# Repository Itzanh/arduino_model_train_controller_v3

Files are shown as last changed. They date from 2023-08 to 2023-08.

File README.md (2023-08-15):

# Arduino Model Train Controller V3

**IMPORTANT: WORK IN PROGRESS**

Arduino Model Train Controller is a program that controls model trains and adds full remote train traffic control: zone blocking, control of the switches, and manual control of the trains. This program focuses on controlling basic model trains modified by adding an Arduino Nano or similar flashed with this software to give the Arduino full control of the model train. This would allow the user to have the full functionality of a remote-controller rail-powered model train in a basic battery-powered model train with no remote control capabilities built-in that has been modified with this software.

The required components to modify the model train are:
- Arduino Nano (or similar)
- HC-05: Bluetooth module that keeps the Arduino in contact with the computer
- L293D chip: to control the built-in motor of the model train
- Reed switch: to detect magnets along the tracks (explained below)
- LED (optional): for train-tracks communication
- Photoresistor (optional): for train-tracks communication

The method to divide the tracks into zones is done by adding small magnets to the tracks (normally by taping them), and attaching a reed switch to the bottom of the model trains. The computer software knows where the trains are because every time they encounter a magnet, they notify the computer and the computer counts the magnets.

## Architecture

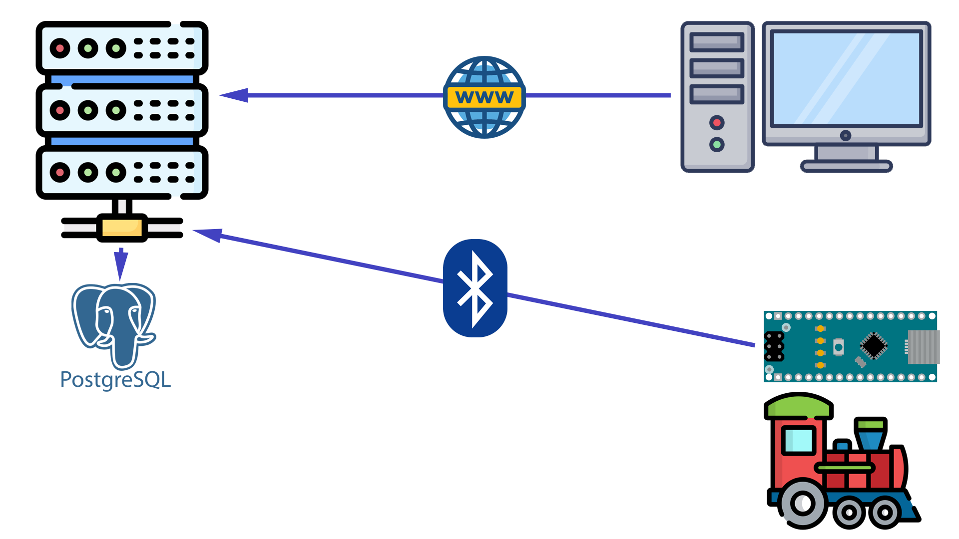
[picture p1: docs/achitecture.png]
graph of the architecture described below


This software is divided in three parts: the server, the web application, and the Arduino sketch.

The server is made with GoLang, and it does all the heavy thinking to control the traffic of the trains. It receives connections from the web application and from the model trains. This server requires to have PostgreSQL installed to work.

The web application is made with react, it connects to the server through WebSocket and allows the end user to dispatch trains and control traffic, among other things.

The Arduino sketch is made to be run in an Arduino Nano or similar, and expects a specific pinout and connections. This is described in the "Modifying the toy train" section below. This software must be flashed to the microcontroller using the Arduino IDE.

## Software installation

### Installing PostgreSQL

Download and install PostgreSQL in your system, create a new database and create a user with access to the database.

### Installing the server

Browse to the server's root folder and run the following command:

```bash
go build -o main.exe | .\main.exe
```

### Installing the web application

Browse to the web application's root folder and run the following command:

```bash
npm run-script build
```

And copy the contents of the "build" folder into a web server's root folder.

### Setting up the trains, zones and signals

#### Set up the trains

Go into the web application into the Trains tab. Use the add button to add as much trains are you are going to use. The three speeds are between 1 and 255, and have to follow this rule: 1 <= slow < half < fast <= 255. In this speeds, 1 means the slowest speed that the train can go (set by the *MOTOR_MIN_POWER* constant explained below) and 255 means the fastest speed that the train can go (set by the *MOTOR_MAX_POWER* constant explained below).

#### Set up the stretches

Stretches are separate zones of tracks, normally independent areas interconnected by switches. Stretches can be set up from the Stretches tab in the web application, added using the add button.

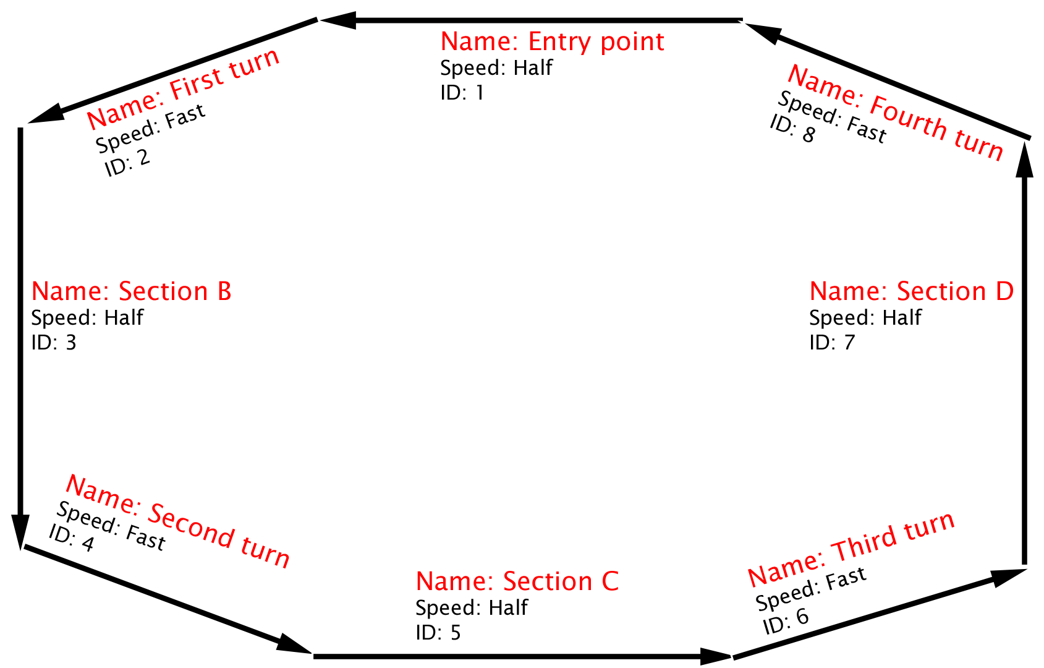
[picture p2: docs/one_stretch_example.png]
example of a circuit with only one stretch


For example, in the model above there is only one stretch.

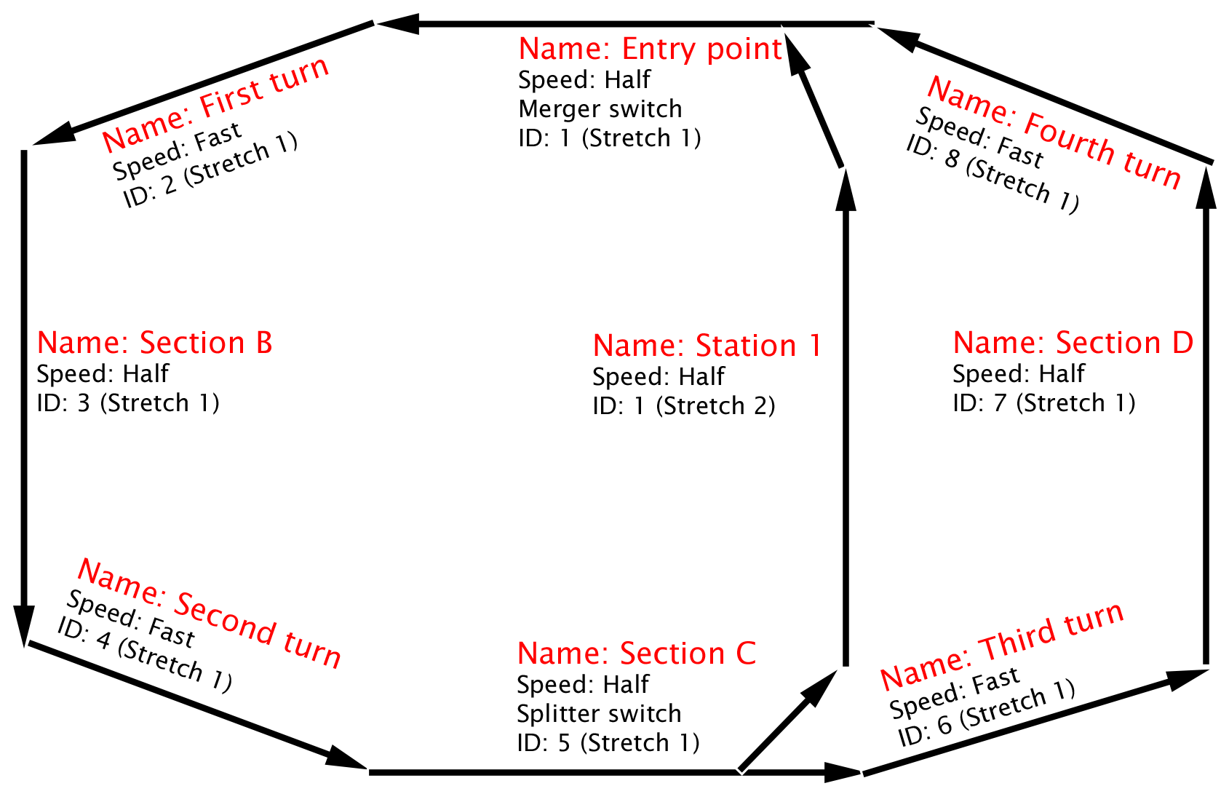
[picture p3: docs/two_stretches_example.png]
example of a circuit with two stretch


For example, in the model above there are two stretches, separated by switches.

#### Set up the signals

Signals are like semaphores, they are used to keep the trains from entering zones occupied by other trains.
When a train put in the model, the user has to manually input the zone that the train is left at, and then the software will keep tracks of where the train is by counting the times that the train reports magnets in the tracks. Every time a train detects a magnet, it passes a signal (or semaphore), therefore there have to be registered as many signals in the program as magnets there are in the tracks.

The way that the software will use this is that only one train at a time will be allowed in the zone between two magnets. If a train steps on a magnet, and the next zone is occupied, the software tells the train to stop and when the zone is freed, it automatically tells the stopped train to start again.

Also different zones can have different speed limits, set by the user, that will automatically be sent from the software to the trains.

The distance between the magnets can never be lower than the maximum length that is expected from a train, as the software considers that, when the train enters a new zone, it has therefore completely exited the zone where it was before and is available to be occupied by another train.

Additionally, some of the zones can be set up as switches, which can be splitters or mergers. In the case of setting the zone as a splitter, the stretch and signal id required will be the signal to which the train will be sent to in case that the switch is flipped to the detour position. In case that it's set as a merger (not splitter), the stretch and signal id required will be the signal from which it will merge from in case that the switch is flipped to the detour position.

In case that your circuit is a loop, you can set a signal to loop back to another signal by entering the required stretch and signal id.

## Hardware

### Modifying the toy train

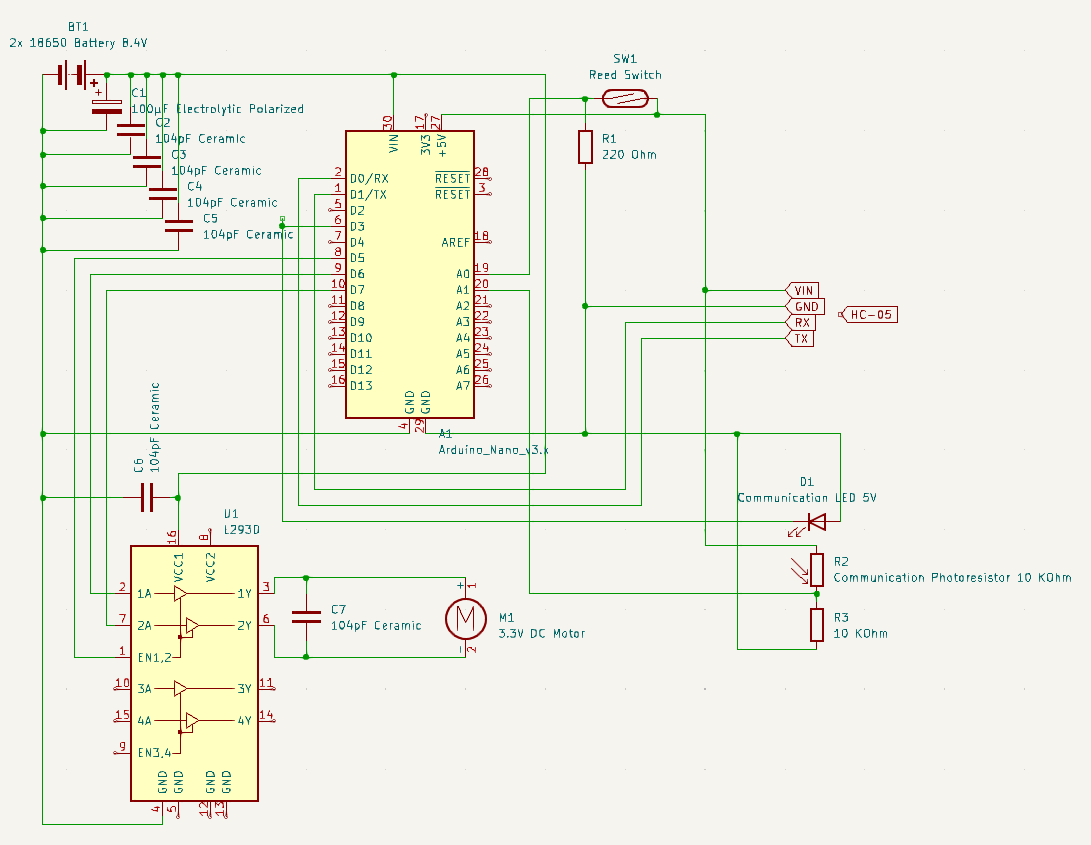
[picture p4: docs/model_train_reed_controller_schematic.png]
Schematic of the model train circuit controller


Schematics are provided in the docs folder of the circuit that the included sketch expects.

In this schematic, the power supply are two 18650 rechargeable lithium-ion batteries (recommended) (BT1), that provide a voltage of 8.4V when fully charged. This is fed directly to the VIN and GND pins of the Arduino (A1), and to the VCC1 and GND pins of the L293D (U1, motor controller chip).

Pinout for the L293D chip:

| L293D pin | Connection |
|---|---|
| PIN#1 | Arduino PIN D5 |
| PIN#2 | Arduino PIN D6 |
| PIN#3 | Toy train motor + |
| PIN#4 | Battery ground |
| PIN#6 | Toy train motor - |
| PIN#7 | Arduino PIN D7 |
| PIN#8 | 8.4V from the battery |

The capacitors are optional, but the ceramic ones are recommended in order to reduce the noise generated by the motor. The values might be others as long as they are reasonable.

The reed switch (SW1) must be placed (for example, taped) to the bottom of the train, in order for it to detect the magnets the are along the tracks. One side of the reed switch has to be connected to 5V (or the logic level of the microcontroller used), and the other side has to be connected to the analog pin #0 of the microcontroller and tied to ground though a resistor (R1) (anything between 100 to 1.000 Ohm should work).

The HC-05 Bluetooth module has to be connected to 5V (or the logic level of the microcontroller used) and ground (shared with the microcontroller's ground). Then, the microcontroller's serial TX pin has to be connected to the HC-05's RX, and vice versa. The HC-05 Bluetooth module has to be set to a UART baud rate of 57.600 beforehand. If you don't know how to do this or don't want to do it, you can also set the constant *SERIAL_BAUD_RATE* to 9.600 (default for the HC-05) in the sketch.

Optionally, the train has the ability to use LED blinks to communicate with other microcontrollers in the tracks that controls the switches, as it's described in the "Making the switch controllers" section below. The negative side of the LED (D1) has to be connected to ground (shared with the microcontroller's ground), and the positive side of the LED has to be connected to the microcontroller's D3 pin. The LED shouldn't need a resistor, because it's only going to be used momentarily, and also because we want it as bright as possible to communicate with the other microcontroller. Then, one side of the photoresistor (R2) has to be connected to 5V (or the logic level of the microcontroller used), and the other side has to be connected to the analog pin #1 of the microcontroller and tied to ground though a 10 KOhmn resistor (R3).

#### Adjusting the constants

- ACCESS_KEY: Key given by the web application when a train is registered.
- MOTOR_MAX_POWER: Number between 0 and 255. You can get it by using the following formula:
```
(Battery voltage / 255) * MOTOR_MAX_POWER = Motor voltage
```
For example, to run a 3V (2xAA battery) train with 2x 18650 batteries, MOTOR_MAX_POWER should be set to 91.
- MOTOR_MIN_POWER: Number between 0 and 255. Should always be lower than *MOTOR_MAX_POWER*. This is the lowest voltage at which the train will run for its lowest speed.
- THRESHOLD_UPPER: Used to detect the LED blinks with the photoresistor. The value reported by the ADC must be above this level to detect a HIGH level in the LED. The default value (800) is selected with a 10-bit ADC in mind.
- THRESHOLD_LOWER: Used to detect the LED blinks with the photoresistor. The value reported by the ADC must be below this level to detect a LOW level in the LED. The default value (400) is selected with a 10-bit ADC in mind.

### Making the switch splitteer controllers

Switch controllers are devices that be placed along the switches in the tracks and control the direction of a switch. They receive commands and communicate with the train using LEDs and photoresistors. In order to flip a switch, the software in the computer has to order the train to flip the switch, then the train will send the command to flip (either to the straight or detour position) to the switch controller via an LED aboard the train, and the blinks of the LED will be picked up by the photoresistor of the switch controller. Once the operation is completed, or if it fails, the switch controller will report it back to the train using the controller's LED and the train's photoresistor, so that the train can report that status back to the software in the computer.

These switch controllers have to be placed in front of where the LED and photoresistor are going to be with the train stopped at the magnet just before the switch, so the LEDs from one and the photoresistors of the other are face to face.

#### Communication protocol

All the messages sent through the LEDs follow a pattern of: ON, OFF, ON, OFF, and the time that the LED has spent ON the first time, then the time that it has spent OFF, and finally the time that is has spent ON the second time, will tell what message has been transmitted.

Messages that the train can transmit:

| Message | Time ON μs | Time OFF μs | Time ON μs |
|---|---|---|---|
| Switch to straight | 500.000 | 500.000 | 500.000 |
| Switch to detour | 1.500.000  | 1.500.00 | 1.500.000  |

Messages that the switch can transmit:

| Message | Time ON μs | Time OFF μs | Time ON μs |
|---|---|---|---|
| Switching successful | 500.000 | 1.500.000 | 500.000 |
| Switching failed | 1.500.000  | 500.00 | 1.500.000  |

It is recommended that a margin of error is applied, detecting everything between 300.000μs to 700.000μs as 500.000μs, and everything from 1.300.000μs to 1.700.000μs as 1.500.000μs. Also a 5s timeout during the message reception is recommended.

#### Manual controllers

Manual switch controllers are a type of switch controllers that can't physically flip the switch in the tracks, so they just take the order and turn on an LED to tell the user that the switch is to be flipped, and then the user has to manually actuate the switch and press a push button so the manual switch controller can send the successful command back to the train.

Required hardware:
- 1x Photoresistor
- 4x LED
- 1x Button
- 1x 10KOhm resistor
- 3x 220Ohm resistor

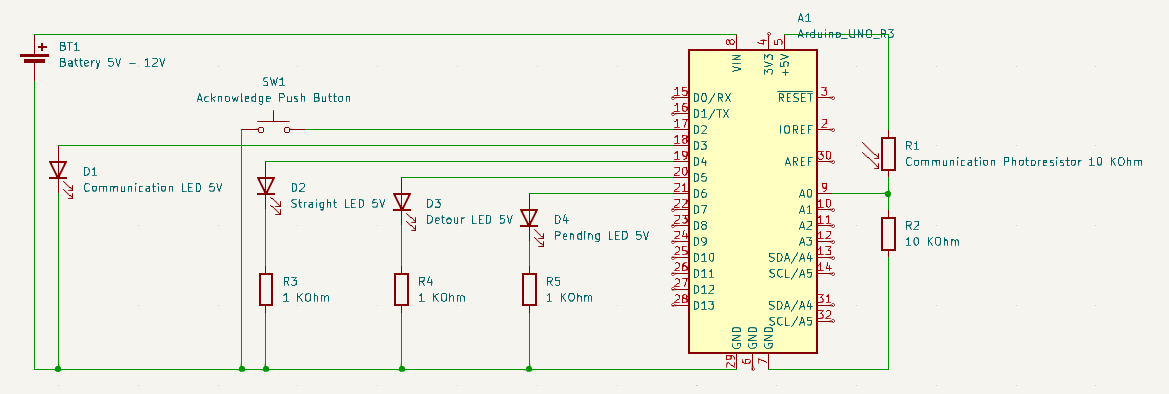
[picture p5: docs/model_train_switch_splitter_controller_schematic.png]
Schematics of the manual switch controller described below


Schematics are provided in the docs folder of the circuit that the included sketch expects.

The power supply may be everything that can power up your microcontroller, although because it has to be made easy to be portable in order to be placed and removed from the tracks easily, a 9V battery or a case with AA batteries might be a good power supply.

The negative side of the LED (D1) has to be connected to ground (shared with the microcontroller's ground), and the positive side of the LED has to be connected to the microcontroller's D3 pin. The LED shouldn't need a resistor, because it's only going to be used momentarily, and also because we want it as bright as possible to communicate with the other microcontroller. Then, one side of the photoresistor (R1) has to be connected to 5V (or the logic level of the microcontroller used), and the other side has to be connected to the analog pin #0 of the microcontroller and tied to ground though a 10 KOhmn resistor (R2).

A push button has to be connected from the microcontroller's D2 pin to ground. This will be the acknowledge button, that the user will have to press once the user has manually actuated the switch.

The pins D4, D5 and D6 will be connected to the positive sides of three LEDs that will be connected to ground through 3 220 Ohm resistors (although anything between 100 to 1.000 Ohm should work fine).

The LED connected to D4 will be the "straight" LED, and will tell the user that the switch is in the "straight position", and the one on D5 will be the "detour" LED to tell the user that this is the position that the switch is in. The LED connected to D6 will be the "needs to be switched" or "pending" LED. If the "pending" LED is on, then the position shown by the first two LEDs is the position that the switch **wants to be**, for example, if both the D4 ad D6 are lit, that means that the user has to move the switch to the straight position and press the acknowledge button.

#### Servomotor controllers

**WORK IN PROGRESS**

#### Stepper motor controllers

**WORK IN PROGRESS**

#### Solenoid motor controllers

**WORK IN PROGRESS**

### Making the switch merger controllers

#### Manual controllers

**WORK IN PROGRESS**

#### Servomotor controllers

**WORK IN PROGRESS**

#### Stepper motor controllers

**WORK IN PROGRESS**

#### Solenoid motor controllers

**WORK IN PROGRESS**

## Contributing

Pull requests are welcome. For major changes, please open an issue first
to discuss what you would like to change.

Please make sure to update tests as appropriate.

## Attribution

Some images and icons are from FlatIcon at [flaticon.com](flaticon.com).

## License

This code is distributed under the [AGPL](https://spdx.org/licenses/AGPL-3.0-only.html) license (AGPL-3.0-only).

You can find the full text of this license in the `COPYING` file.

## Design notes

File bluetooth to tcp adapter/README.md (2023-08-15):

# Model Train Controller

Open Model Train Controller is a software that can control different types of model trains from a computer through a browser, letting you become a “train dispatcher" of you model.

This software can control the signals of the model through microcontroller units (like Arduino, etc.) that are connected then to the computer. This software is entirely open source and free software published under the GNU AGPL license.

The code for the web dispatching interface, the server, and the code necessary for the microcontroller units are included in the repositories.

## Links

[Wiki - Documentation](http://izcloud.tk:5000/en/home)

[Model Train Controller Server Repository](https://gitlab.com/itzanh/model-train-controller-server)

[Model Train Controller Web Repository](https://gitlab.com/itzanh/model-train-controller-web)

[Model Train Controller Repository](https://gitlab.com/itzanh/model-train-controller)

[Model Train Controller Signal Controller Repository](https://gitlab.com/itzanh/model-train-controller-signal-controller)

[Model Train Controller Serial to TCP Repository](https://gitlab.com/itzanh/model-train-controller-serial-to-tcp)

[Model Train Controller I2C to Serial Repository](https://gitlab.com/itzanh/model-train-controller-i2c-to-serial)

## Contributing
Pull requests are welcome. For major changes, please open an issue first to discuss what you would like to change.

## License

This code is distributed under the [AGPL](https://spdx.org/licenses/AGPL-3.0-only.html) license (AGPL-3.0-only).

You can find the full text of this license in the `COPYING` file.

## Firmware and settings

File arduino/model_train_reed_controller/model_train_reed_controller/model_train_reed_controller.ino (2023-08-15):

/*
This file is part of Arduino Model Train Controller V3 (https://github.com/Itzanh/arduino_model_train_controller_v3).

Arduino Model Train Controller V3 is free software: you can redistribute it and/or modify it under the terms of the GNU Affero General Public License as published by the Free Software Foundation, version 3 of the License.

Model Train Controller is distributed in the hope that it will be useful, but WITHOUT ANY WARRANTY; without even the implied warranty of MERCHANTABILITY or FITNESS FOR A PARTICULAR PURPOSE. See the GNU Affero General Public License for more details.

You should have received a copy of the GNU Affero General Public License along with Model Train Controller. If not, see <https://www.gnu.org/licenses/>.
*/

// This sketch is made to be run on an Arduino Nano, with the objective to to control a model train, controlling its onboard-motor with a L293D-chip, detecting its position
// in the tracks using magnets left along the way in the tracks in specific positions, and receiving instructions for traffic control and signaling from a computer software
// that keeps communication with the Nano through a HC-05 Bluetooth module.
//
// Pinout description: (ARDUINO UNO / NANO)
// DIGITAL:
// 2
// 3 } - Communication LED
// 4
// 5   } - L293D - { Enable (~PWM) 10Ohm
// 6   }           { DIR_B 5.2KOhm
// 7   }           { DIR_A 5.2KOhm
// 8
// 9
// 10
// 11
// 12
// 13
// A0 } - Reed switch 5V / 220Ohm to GND
// A1 } - Photoresistor 5V / 10KOhm to GND
// TX -> HC-05 RX
// RX -> HC-05 TX



// Constants
const unsigned long ACCESS_KEY = 2107106630;
// const unsigned long ACCESS_KEY = 2086438159;
// const byte MOTOR_MAX_POWER = 100;
// const byte MOTOR_MIN_POWER = 85;
// const byte MOTOR_MAX_POWER = 120;
// const byte MOTOR_MIN_POWER = 85;
// const byte MOTOR_MAX_POWER = 190;
// const byte MOTOR_MIN_POWER = 85;
const byte MOTOR_MAX_POWER = 255;
const byte MOTOR_MIN_POWER = 85;
// const byte MOTOR_MIN_POWER = 200;
const float MAX_SPEED_LIMIT = 255;
const unsigned short SOFTWARE_DEBOUNCING_WAIT = 250; // ms
const unsigned short SERIAL_BAUD_RATE = 57600;
const unsigned short THRESHOLD_UPPER = 800;
const unsigned short THRESHOLD_LOWER = 400;

// DEFINE PINOUT
// Digital
const byte COMMUNICATION_LED_PIN = 3;
const byte MOTOR_ENABLE_PIN = 5;
const byte MOTOR_DIR_A_PIN = 6;
const byte MOTOR_DIR_B_PIN = 7;
// Analog
const byte REED_SWITCH_PIN = A0;
const byte ANALOG_PHOTORESISTOR_PIN = A1;



// Variables
volatile bool reedSwitchClosed = false;
volatile long lastReedSwitchClosedTime = 0;



enum CommunicationMessageServerToClient {
  FORWARD = 1,
  BACKWARD = 2,
  FAST_STOP = 3,
  SWITCH_PASSTHROUGH = 4,
  SWITCH_DETOUR = 5,
};

enum CommunicationMessageClientToServer {
  REED_TRIGGERED = 1,
  SWITCH_SUCCESS = 2,
  SWITCH_FAILURE = 3,
};

void setup()
{
  pinMode(COMMUNICATION_LED_PIN, OUTPUT);

  // Initialize the pins for the L293D motor controller
  pinMode(MOTOR_ENABLE_PIN, OUTPUT);
  pinMode(MOTOR_DIR_A_PIN, OUTPUT);
  pinMode(MOTOR_DIR_B_PIN, OUTPUT);

  // Open a (hardware) serial connection with the HC-05 BlueTooth module
  Serial.begin(SERIAL_BAUD_RATE);
  // Log in the the ground control software through BlueTooth
  blueToothLogin();
}

void blueToothLogin()
{
  // When the ground control server is ready, it sends a byte of all ones (255) and awaits for the token
  // Wait for the "ready" byte to come
  while (Serial.available() == 0) {}
  Serial.read();
  // Send the authentication token
  Serial.write((byte*)&ACCESS_KEY, sizeof(unsigned long));
}

void loop()
{
  if (reedSwitchClosed)
  {
    reedSwitchClosed = analogRead(REED_SWITCH_PIN) >= 256;
  }
  else
  {
    if ((analogRead(REED_SWITCH_PIN) > 512) && (millis() - lastReedSwitchClosedTime > 1000))
    {
      Serial.write(1);
      Serial.write(CommunicationMessageClientToServer::REED_TRIGGERED);
      reedSwitchClosed = true;
      lastReedSwitchClosedTime = millis();
    }
  }

  while (Serial.available())
  {
    receiveIncomingCommunicationMessage();
  }
}

void receiveIncomingCommunicationMessage()
{
  byte size = Serial.read();
  byte message[size];

  for (byte i = 0; i < size; i++) {
    int b = Serial.read();
    if (b == -1)
    {
      i--;
    }
    else
    {
      message[i] = b;
    }
  }

  processIncomingMessage(message);
}

void processIncomingMessage(byte message[])
{
  switch (message[0])
  {
    case CommunicationMessageServerToClient::FORWARD:
      {
        goForward(message[1]);
        break;
      }
    case CommunicationMessageServerToClient::BACKWARD:
      {
        goBackwards(message[1]);
        break;
      }
    case CommunicationMessageServerToClient::FAST_STOP:
      {
        fastStop();
        break;
      }
    case CommunicationMessageServerToClient::SWITCH_PASSTHROUGH:
      {
        switchToPassthrough();
        break;
    } case CommunicationMessageServerToClient::SWITCH_DETOUR:
      {
        switchToDetour();
        break;
      }
  }
}

void goForward(byte speedLimit)
{
  lastReedSwitchClosedTime = millis();
  byte motorSpeed = convertSpeedLimitToMotorSpeed(speedLimit);
  analogWrite(MOTOR_ENABLE_PIN, motorSpeed);
  digitalWrite(MOTOR_DIR_A_PIN, HIGH);
  digitalWrite(MOTOR_DIR_B_PIN, LOW);
}

void goBackwards(byte speedLimit)
{
  lastReedSwitchClosedTime = millis();
  byte motorSpeed = convertSpeedLimitToMotorSpeed(speedLimit);
  analogWrite(MOTOR_ENABLE_PIN, motorSpeed);
  digitalWrite(MOTOR_DIR_A_PIN, LOW);
  digitalWrite(MOTOR_DIR_B_PIN, HIGH);
}

void fastStop()
{
  analogWrite(MOTOR_ENABLE_PIN, 255);
  digitalWrite(MOTOR_DIR_A_PIN, LOW);
  digitalWrite(MOTOR_DIR_B_PIN, LOW);
}

byte convertSpeedLimitToMotorSpeed(byte speedLimit)
{
  float relativeSpeed = float(speedLimit) / MAX_SPEED_LIMIT;
  return MOTOR_MIN_POWER + (relativeSpeed * (MOTOR_MAX_POWER - MOTOR_MIN_POWER));
}

void switchToPassthrough() {
  digitalWrite(COMMUNICATION_LED_PIN, HIGH);
  delay(500);
  digitalWrite(COMMUNICATION_LED_PIN, LOW);
  delay(500);
  digitalWrite(COMMUNICATION_LED_PIN, HIGH);
  delay(500);
  digitalWrite(COMMUNICATION_LED_PIN, LOW);

  processLEDResponse();
}

void switchToDetour() {
  digitalWrite(COMMUNICATION_LED_PIN, HIGH);
  delay(1500);
  digitalWrite(COMMUNICATION_LED_PIN, LOW);
  delay(1500);
  digitalWrite(COMMUNICATION_LED_PIN, HIGH);
  delay(1500);
  digitalWrite(COMMUNICATION_LED_PIN, LOW);

  processLEDResponse();
}

void processLEDResponse()
{
  if (waitForLEDResponse())
  {
    Serial.write(1);
    Serial.write(CommunicationMessageClientToServer::SWITCH_SUCCESS);
  }
  else
  {
    Serial.write(1);
    Serial.write(CommunicationMessageClientToServer::SWITCH_FAILURE);
  }
}

bool waitForLEDResponse() {
  // Wait for it to go HIGH
  /*do {

    } while (analogRead(ANALOG_PHOTORESISTOR_PIN) <= THRESHOLD_LOWER);*/
  do {

  } while (analogRead(ANALOG_PHOTORESISTOR_PIN) <= THRESHOLD_UPPER);
  // It went HIGH, note the time and wait for it to go LOW again
  unsigned long startMicros = micros();
  unsigned long timeoutMillis = millis() + 5000;
  do {
    if (millis() >= timeoutMillis) {
      // Serial.println("TIMEOUT 1");
      /*Serial.write(3);
      Serial.write(128);
      Serial.write("F");
      Serial.write(1);*/
      return false;
    }
  } while (analogRead(ANALOG_PHOTORESISTOR_PIN) <= THRESHOLD_UPPER);
  do {
    if (millis() >= timeoutMillis) {
      // Serial.println("TIMEOUT 2");
      /*Serial.write(3);
      Serial.write(128);
      Serial.write("F");
      Serial.write(2);*/
      return false;
    }
  } while (analogRead(ANALOG_PHOTORESISTOR_PIN) >= THRESHOLD_LOWER);
  // It went HIGH and then LOW again
  unsigned long endMicros = micros();
  unsigned long microsPeriod1 = endMicros - startMicros;
  timeoutMillis = millis() + 5000;
  // Wait for it to go HIGH again
  do {
    if (millis() >= timeoutMillis) {
      // Serial.println("TIMEOUT 3");
      /*Serial.write(3);
      Serial.write(128);
      Serial.write("F");
      Serial.write(3);*/
      return false;
    }
  } while (analogRead(ANALOG_PHOTORESISTOR_PIN) <= THRESHOLD_UPPER);
  // It went HIGH again, note the time that it spent LOW and note the start time
  unsigned long microsPeriod2 = micros() - endMicros;
  startMicros = micros();
  timeoutMillis = millis() + 5000;
  do {
    if (millis() >= timeoutMillis) {
      // Serial.println("TIMEOUT 4");
      /*Serial.write(3);
      Serial.write(128);
      Serial.write("F");
      Serial.write(4);*/
      return false;
    }
  } while (analogRead(ANALOG_PHOTORESISTOR_PIN) >= THRESHOLD_LOWER);
  // It went HIGH and then LOW again
  endMicros = micros();
  unsigned long microsPeriod3 = endMicros - startMicros;

  if ((microsPeriod1 > 300000) && (microsPeriod1 < 700000) && (microsPeriod2 > 1300000) && (microsPeriod2 < 1700000) && (microsPeriod3 > 300000) && (microsPeriod3 < 700000)) {
    // Acknowledgement
    return true;
  }
  // ... else ...
  /*Serial.print("microsPeriod1 ");
    Serial.print(microsPeriod1);
    Serial.print(" microsPeriod2 ");
    Serial.print(microsPeriod2);
    Serial.print(" microsPeriod3 ");
    Serial.println(microsPeriod3);*/
  /*Serial.write(15);
  Serial.write(128);
  Serial.write("F");
  Serial.write(5);*/

  /*Serial.write((char*)&microsPeriod1, 4);
  Serial.write((char*)&microsPeriod2, 4);
  Serial.write((char*)&microsPeriod3, 4);*/

  // Non-Acknowlegdement / Error
  return false;
}

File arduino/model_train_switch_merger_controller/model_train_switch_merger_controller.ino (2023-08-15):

/*
This file is part of Arduino Model Train Controller V3 (https://github.com/Itzanh/arduino_model_train_controller_v3).

Arduino Model Train Controller V3 is free software: you can redistribute it and/or modify it under the terms of the GNU Affero General Public License as published by the Free Software Foundation, version 3 of the License.

Model Train Controller is distributed in the hope that it will be useful, but WITHOUT ANY WARRANTY; without even the implied warranty of MERCHANTABILITY or FITNESS FOR A PARTICULAR PURPOSE. See the GNU Affero General Public License for more details.

You should have received a copy of the GNU Affero General Public License along with Model Train Controller. If not, see <https://www.gnu.org/licenses/>.
*/

const unsigned short THRESHOLD_UPPER = 800;
const unsigned short THRESHOLD_LOWER = 400;

const byte ANALOG_PHOTORESISTOR_STRAIGHT_PIN = A0;
const byte ANALOG_PHOTORESISTOR_DETOUR_PIN = A1;
const byte ACKNOWLEDGE_DIRECTION_BUTTON_PIN = 2;
const byte COMMUNICATION_LED_STRAIGHT_PIN = 3;
const byte COMMUNICATION_LED_DETOUR_PIN = 4;
const byte STRAIGHT_DIRECTION_LED_PIN = 5;
const byte DETOUR_DIRECTION_LED_PIN = 6;
const byte CHANGE_DIRECTION_LED_PIN = 7;

bool switchPosition = true; // True = straight, False = detour
bool switchRequestFrom = true; // True = straight, False = detour
volatile bool acknowledged = true;



void setup() {
  Serial.begin(1000000);

  pinMode(COMMUNICATION_LED_STRAIGHT_PIN, OUTPUT);
  pinMode(COMMUNICATION_LED_DETOUR_PIN, OUTPUT);
  pinMode(STRAIGHT_DIRECTION_LED_PIN, OUTPUT);
  pinMode(DETOUR_DIRECTION_LED_PIN, OUTPUT);
  pinMode(CHANGE_DIRECTION_LED_PIN, OUTPUT);
  pinMode(ACKNOWLEDGE_DIRECTION_BUTTON_PIN, INPUT_PULLUP);

  attachInterrupt(digitalPinToInterrupt(ACKNOWLEDGE_DIRECTION_BUTTON_PIN), acknowledgeButtonPressed, FALLING);

  printSwitchPosition(true);
}

void acknowledgeButtonPressed() {
  printSwitchPosition(true);
  acknowledged = true;
}

void loop() {
  if (!acknowledged) {
    do {

    } while (!acknowledged);
    sendAcknowledgement(switchRequestFrom ? COMMUNICATION_LED_STRAIGHT_PIN : COMMUNICATION_LED_DETOUR_PIN);
  }

  // Wait for it to go HIGH
  if (analogRead(ANALOG_PHOTORESISTOR_STRAIGHT_PIN) > THRESHOLD_LOWER) {
    switchRequestFrom = true;
    receiveSignal(ANALOG_PHOTORESISTOR_STRAIGHT_PIN, COMMUNICATION_LED_STRAIGHT_PIN);
  }
  if (analogRead(ANALOG_PHOTORESISTOR_DETOUR_PIN) > THRESHOLD_LOWER) {
    switchRequestFrom = false;
    receiveSignal(ANALOG_PHOTORESISTOR_DETOUR_PIN, COMMUNICATION_LED_DETOUR_PIN);
  }
}

void receiveSignal(byte analogPin, byte communicationLEDpin) {
  // It went HIGH in the loop function, note the time and wait for it to go LOW again
  unsigned long startMicros = micros();
  unsigned long timeoutMillis = millis() + 5000;
  do {
    if (millis() >= timeoutMillis) {
      return;
    }
  } while (analogRead(analogPin) <= THRESHOLD_UPPER);
  do {
    if (millis() >= timeoutMillis) {
      return;
    }
  } while (analogRead(analogPin) >= THRESHOLD_LOWER);
  // It went HIGH and then LOW again
  unsigned long endMicros = micros();
  unsigned long microsPeriod1 = endMicros - startMicros;
  timeoutMillis = millis() + 5000;
  // Wait for it to go HIGH again
  do {
    if (millis() >= timeoutMillis) {
      return;
    }
  } while (analogRead(analogPin) <= THRESHOLD_UPPER);
  // It went HIGH again, note the time that it spent LOW and note the start time
  unsigned long microsPeriod2 = micros() - endMicros;
  startMicros = micros();
  timeoutMillis = millis() + 5000;
  do {
    if (millis() >= timeoutMillis) {
      return;
    }
  } while (analogRead(analogPin) >= THRESHOLD_LOWER);
  // It went HIGH and then LOW again
  endMicros = micros();
  unsigned long microsPeriod3 = endMicros - startMicros;

  if ((microsPeriod1 > 300000) && (microsPeriod1 < 700000) && (microsPeriod2 > 300000) && (microsPeriod2 < 700000) && (microsPeriod3 > 300000) && (microsPeriod3 < 700000)) {
    // Signal 1
    changeSwitchPosition(true);
  } else if ((microsPeriod1 > 1300000) && (microsPeriod1 < 1700000) && (microsPeriod2 > 1300000) && (microsPeriod2 < 1700000) && (microsPeriod3 > 1300000) && (microsPeriod3 < 1700000)) {
    // Signal 2
    changeSwitchPosition(false);
  } else {
    sendNonAcknowledgement(communicationLEDpin);
  }
}

void changeSwitchPosition(bool newSwitchPosition) {
  if (switchPosition == newSwitchPosition) {
    sendAcknowledgement(switchRequestFrom ? COMMUNICATION_LED_STRAIGHT_PIN : COMMUNICATION_LED_DETOUR_PIN);
    return;
  }

  switchPosition = newSwitchPosition;
  acknowledged = false;
  printSwitchPosition(false);
}

void printSwitchPosition(bool acknowledged) {
  if (switchPosition) {
    digitalWrite(STRAIGHT_DIRECTION_LED_PIN, HIGH);
    digitalWrite(DETOUR_DIRECTION_LED_PIN, LOW);
  } else {
    digitalWrite(STRAIGHT_DIRECTION_LED_PIN, LOW);
    digitalWrite(DETOUR_DIRECTION_LED_PIN, HIGH);
  }
  if (acknowledged) {
    digitalWrite(CHANGE_DIRECTION_LED_PIN, LOW);
  } else {
    digitalWrite(CHANGE_DIRECTION_LED_PIN, HIGH);
  }
}

void sendAcknowledgement(byte pin) {
  digitalWrite(pin, HIGH);
  delay(500);
  digitalWrite(pin, LOW);
  delay(1500);
  digitalWrite(pin, HIGH);
  delay(500);
  digitalWrite(pin, LOW);
}

void sendNonAcknowledgement(byte pin) {
  digitalWrite(pin, HIGH);
  delay(1500);
  digitalWrite(pin, LOW);
  delay(500);
  digitalWrite(pin, HIGH);
  delay(1500);
  digitalWrite(pin, LOW);
}
